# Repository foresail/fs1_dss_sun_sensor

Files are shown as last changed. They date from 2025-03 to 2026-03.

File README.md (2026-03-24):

# Foresail-1 DSS Sun Sensor

This repository contains the public available design files for the DSS sun sensor designed for the Foresail-1 Cubesat.

The performance and testing of this sensor has been documented in [this article](https://doi.org/10.1016/j.asr.2026.01.083).

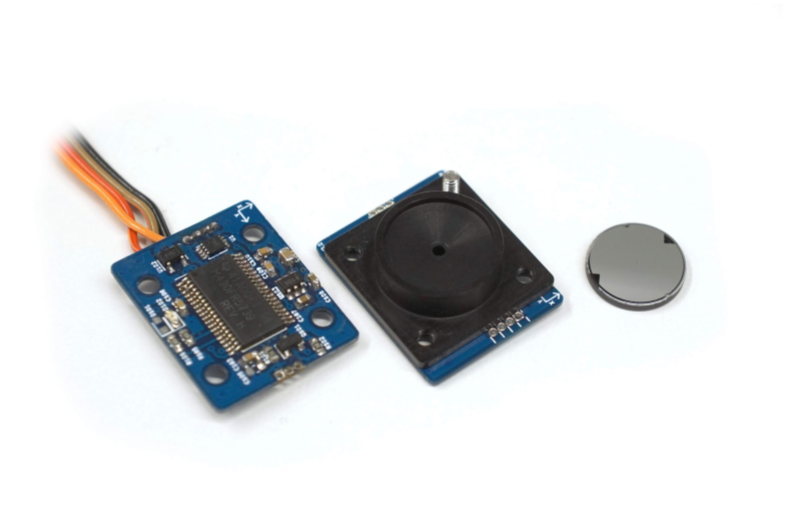
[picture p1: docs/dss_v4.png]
DSS Sun Sensor v4


The general characteristics of sensor design are:
- Dimensions: 20.4 mm × 24.8 mm × 7 mm
- Mass: 4.4 grams
- Panel mountedable into 14x14 mm hole with two M2 screws.
- Electrical connection by soldering on the panel PCB or by harness.
- FOV: ~30 degrees, resolution: 0.027°, accuracy: ±0.008°
- Refresh rate up to 38 Hz. (Sampling time: 15 ms + communication overhead)
- Can provide following data products:
    - Raw current measurements
    - Point & intensity measurements
    - Sun vector & intensity measurements
    - Angles & intensity measurements
- I2C digital serial interface (hardware version 4)
- RS-485 digital interface (hardware version 5)
- Low power consumption < 4 mW when active
- Nominal operating voltage: 3.6 - 3.8V: Can be extened easily to 2.0 – 5.5 V.

## Documentation

- [Research Paper](https://doi.org/10.1016/j.asr.2026.01.083)
- [FS1 ADCS DSS Sun Sensor Design Document](docs/FS1p_ADCS_DSS_Digital_Sun_Sensor_Hardware_Design.pdf)
- [Version 4 schematic (I2C variant)](v4/dss_v4_schema.pdf)
- [Version 4 firmware source code](v4/fw)
- [Version 5 schematic (RS-485 variant)](v5/dss_v5_schema.pdf)
- [Version 5 firmware source code](v5/fw)
- [Calibration and test tools for PC](calibration)
- [Mechanical design files](mechanical)

## Licence

The design is licenced under [CERN Open Hardware Licence Version 2](LICENCE)

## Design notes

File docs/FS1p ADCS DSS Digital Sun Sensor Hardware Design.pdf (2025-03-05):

## Digital Sun Sensor

Hardware Design v5

Responsible: Marius Anger
Version date: 2023-10-18
Page: 1 / 17

# Foresail-1p

# Digital Sun Sensor Hardware Design v5

# Aalto University

## Department of Electronics and Nanoengineering

Page: 2 / 17

### Authors

Name | Worked with parts
Bruce Clayhills | The whole document
Marius Anger | Hardware revision 5

### Table of Contents

1 General | 4
1.1 Scope | 4
1.2 Reference Documents | 4
1.3 Abbreviations and Acronyms | 5
2 Sensor Design | 5
2.1 DSS General Characteristics: | 6
2.2 Mechanical Cover | 6
2.3 ND-Filter & Mask Design | 7
2.4 Theoretical FOV | 8
2.5 Theoretical accuracy | 9
3 Electrical Design | 9
3.1 Microcontroller | 10
3.2 S9132 Profile Sensor | 11
3.3 Power Supply | 11
3.4 Inrush current | 12
3.5 Sensor Gain Selection | 14
3.6 Environment | 15
4 Software | 15
5 Calibration and Validation | 15
Appendices | 17
A. Schematics | 17
B. PCB Layout | 17

Page: 3 / 17

## 1 General

### 1.1 Scope

The purpose of this document is to present the current digital sun sensor design for Foresail-1p. This document is made for the hardware revision 5, and is mainly based on the Hamamatsu S9132 profile sensor.

The design files related to this document and version can be found on the following Github repository:
Revision 1-4: https://github.com/aaltosatellite/foresail/tree/master/dss_sunsensor
Revision 5: https://github.com/aaltosatellite/fs1p_adcs/tree/main/dss_sunsensor

### 1.2 Reference Documents

1. Hamamatsu S9132 Profile Sensor - datasheet: https://www.hamamatsu.com/resources/pdf/ssd/s9132_kmpd1075e.pdf
2. Texas Instrument’s MSP430FR5739 datasheet: http://www.ti.com/lit/ds/symlink/msp430fr5739.pdf
3. FS1 PSD Sun Sensor Design: https://docs.google.com/document/d/1SByVZYXU1UmMgaHT1f_zqc_vpBboQWTH_l9uw-Ily4A/edit# (https://docs.google.com/document/d/1SByVZYXU1UmMgaHT1f_zqc_vpBboQWTH_l9uw-Ily4A/edit#)
4. FS1 ADCS Digital Sun Sensor Software Design Document (https://docs.google.com/document/u/0/d/1WGHVzIKvUKaqTUZvLEAsgHj6r2W2jWne70urNSRBq0A/edit)
5. FS1 ADCS Digital Sun Sensor Test Plan (https://docs.google.com/document/u/0/d/1igoooQxarRuDu3o5K0XlWpgVwwoYvSnRIX3EzYSsQn4/edit)
6. ND Filter:
OD 3.0 VIS, 12.5mm Dia. Non-Reflective ND Filter (https://www.edmundoptics.eu/p/od-30-vis-125mm-dia-non-reflective-nd-filter/17996/)

### 1.3 Abbreviations and Acronyms

ADCS | Attitude Determination and Control System
DSS | Digital Sun Sensor
FOV | Field of View
MCU | MicroController Unit
ND-Filter | Neutral Density Filter
LPM | Low-Power Mode
SEM | Scanning Electron Microscope

Page: 4 / 17

## 2 Sensor Design

The digital sun sensor is based upon the Hamatsu S9132 Profile sensor. This is a CMOS based area sensor, which works with 8bit or 10bit logic (user configurable). In this board, the sensor is configured to use 8bit logic. This can however be changed at a later date with a hardware change to the PCB.

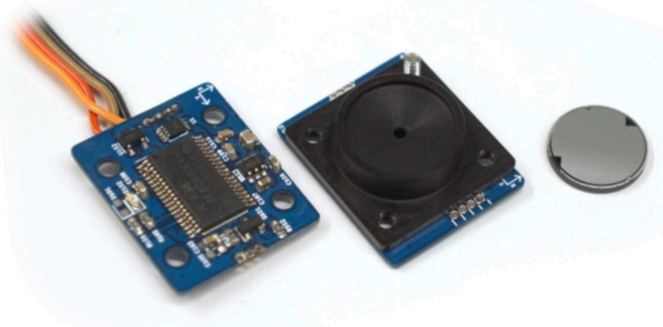
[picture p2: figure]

Figure 1. DSS PCB

The PCB of the DSS board consists of the front side, with the profile sensor, as well as the back side with the MSP430, power circuitry, RS485 transceiver and connectors to external power and programming.

The PCB design also incorporates 4×M2 mounting holes which connect the board to the cover and the hull of the satellite.

### 2.1 DSS General Characteristics:

- Dimensions: 20.4 × 24.8 × 7.0 mm
- Power consumption:
- In use: ≈100 mW
- Standby: ≈5 mW
- FOV: ≈50 degrees (Theoretical)
- Accuracy: ±0.1° (Theoretical)
- Boot up time: ≈500 ms

Page: 5 / 17

- Sampling time: ≈26 ms
- Operating voltage: 3–5 V:
- 5 V charge-pump regulator
- 3.3V LDO
- Serial Communication Interface: RS485
- ND-filter - 0.1 Transmission (%)
- Mask made with optical lithography
- 0.1 mm pinhole

### 2.2 Mechanical Cover

The DSS has an aluminum cover designed with Fusion 360. This mechanical cover provides protection to the S9132 sensor, as well as houses the ND-filter and mask inside. The cover will be made of space grade aluminum, which is anodized black.

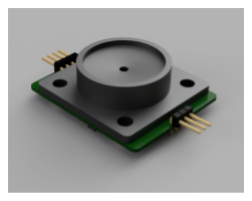
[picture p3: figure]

Figure 3. DSS Cover v4

The mask of the DSS is put on top of the ND-filter. The DSS cover has been designed with minimal tolerances, so that there is little to none excess space for the ND filter to move around. However, the tolerances in the design assume the worst case scenario for the dimensions of the ND-filter and S9132 profile sensor.

To ensure that the ND-filter and mask stays in one spot, the ND-filter will be glued to the aluminum cover using two part space grade epoxy glue. It is important to perform all the testing procedures defined in the FS1 ADCS Digital Sun Sensor Prototype Test Plan (https://drive.google.com/open?id=1igoooQxarRuDu3o5K0XlWpgVwwoYvSnRIX3EzYSsQn4) document after this, to ensure the correct calibration values and proper operation of the sensor.

For the manufacturing of the mechanical structure and the PCB of the sun sensor be sure to take a look at the FS1 ADCS Digital Sun Sensor Manufacturing Guide. (https://drive.google.com/open?id=1_A-BLVwWmDk6d4qx7FV5U0ANPm-P0pnfzcUZG10FYfE)

### 2.3 ND-Filter & Mask Design

The S9132 requires an ND-filter to reduce the intensity of the light hitting the surface of the sensor, otherwise the sensor will saturate and output values of maximum intensity. This results in loss of accuracy, once the center point of the light hitting the surface of the sensor is estimated.

The sensor must be able to withstand the intensity of light in the visual spectrum (to which it is most sensitive) while operating in space. The calculated ND-filter transmittance value should be

Page: 6 / 17

around 0.1, in order to prevent saturation.

This is done with an Edmund Optics OD 3.0 VIS, 12.5mm Dia. Non-Reflective ND Filter, (https://www.edmundoptics.eu/p/od-30-vis-125mm-dia-non-reflective-nd-filter/17996/) with a transmittance value of 0.1. The transmittance value is guaranteed to be within a tolerance of ±0.05% by the manufacturer. This value will also be verified during the EQM and flight model testing and characterization.

The mask design is a simple pinhole in the middle of the ND-filter with a hole of a diameter of 0.1 mm as shown in Figure 4. This shows an incoming incident light hitting the profile sensor surface. The ND-filter also provides additional UV-protection to the profile sensor.

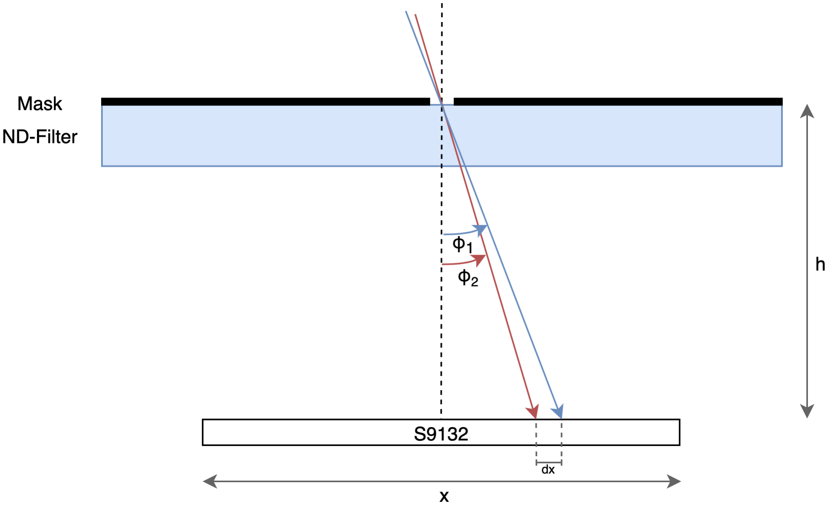
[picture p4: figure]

Figure 4. ND-filter & Mask

The film, which is set on top of the ND-filter, will have a titanium coating laid directly onto the glass surface with optical lithography. The titanium adheres strongly onto the glass layer, providing a strong bond. After this, an additional layer of aluminium will also be set on top of the layer of titanium, in order to provide better resistance to physical damage from sunlight and other sources. The aluminium also adheres better to a titanium surface compared to glass directly.

The diameter of the pinhole can be seen in Figure 5. This is an image taken with a SEM.

Page: 7 / 17

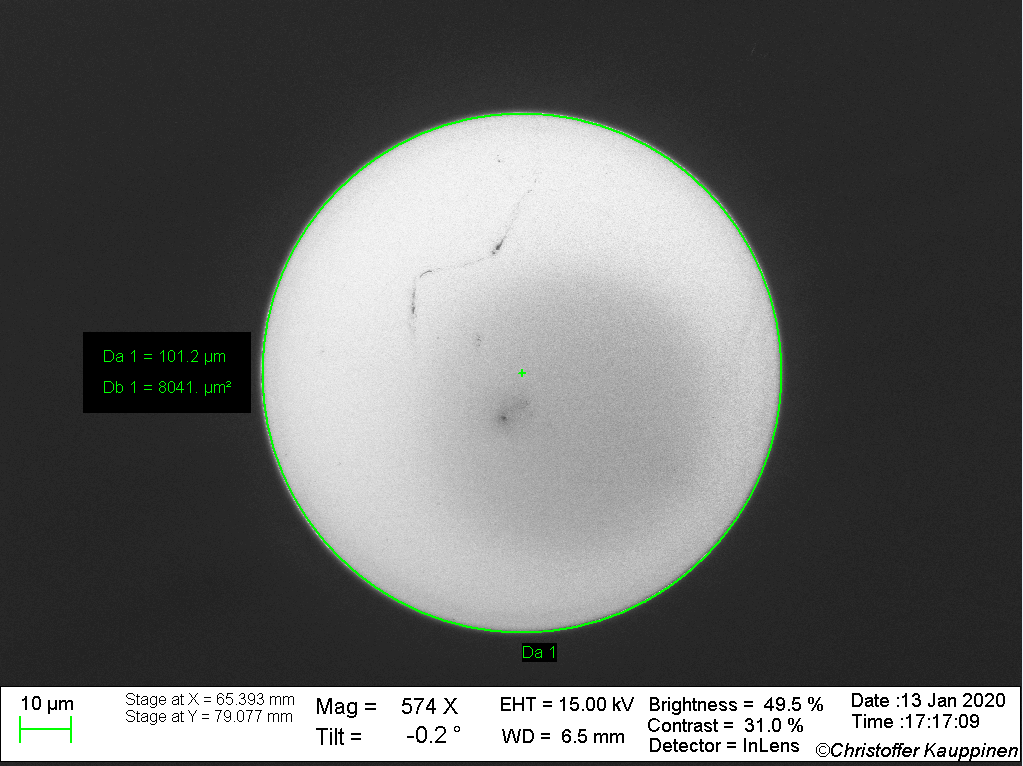
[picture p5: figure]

Figure 5. SEM picture of the pinhole

### 2.4 Theoretical FOV

The field of view (FOV) of a sun sensor is an integral part of its design, and a defining quality of the sensor. Different satellite designs have different requirements that the sun sensors must achieve. There is always a trade-off between the maximum theoretical accuracy and the FOV of a sun sensor.

The selection of the FOV of a sun sensor should be made in conjunction with the selection of the desired accuracy of the sensor. In addition to the theoretical analysis for these properties, one should also take into account the practical limitations of the hardware on the sensor.

The FOV of a pinhole-based sun sensor is affected by the height of the mask from the sensor's surface, the location of the pinhole relative to the center spot of the sensor and the physical constraints of the enclosure. The equation governing the maximum theoretical FOV of a sun sensor is:

, where is the height of the pinhole from the sensor surface and x array length of the sensor.

### 2.5 Theoretical accuracy

Page: 8 / 17

The accuracy of a sun sensor is not a property that should be addressed alone, as the FOV impacts the theoretical accuracy and vice versa. A higher pinhole height leads to a better accuracy, as the FOV is limited. This is because the sensor has a finite amount of pixels, which are used for measurements. So a smaller FOV in theory equates to a better accuracy as the sensor can utilise more pixels to distinguish a variation of one degree.

The linear resolution is the distance in between the individual pixels on the profile sensor. The accuracy of a sun sensor can be derived from the pinhole height and the linear resolution of the
sensor. Referring to Figure 4, the accuracy is the difference between | and , when | is equal to
the linear resolution. This gives us the following relation for the maximum theoretical accuracy:

The equation, which relates the FOV and the accuracy of a sun sensor is:

, where is the array size and is the linear resolution.

Page: 9 / 17

## 3 Electrical Design

The electrical design of the sun sensor has been done in KiCad 5.0. Key design objectives have been a reduced power consumption, and the reliable operation of the sensor board.

### 3.1 Microcontroller

The DSS has a Texas Instruments MSP430FR5739 microcontroller embedded into its design, operated at 24 MHz, which handles data processing and interfacing with the rest of the ADCS on-board the OBC.

If needed, the MCU can also be operated at a lower frequency to reduce power consumption.

MCU characteristics:
- 16-Bit RISC Architecture up to 24-MHz Clock
- –40°C to +85°C Operation
- 16 KB of Nonvolatile FRAM Memory
- RS485 communication protocol
- 2.0 V to 3.6 V operating voltage

The MCU also has an integrated watch-dog timer (WDT), which ensures that the MCU is rebooted if it detects a halt in the main loop if code execution lingers for longer than a certain time period. The WDT will be used to prevent a situation, where the sensor becomes unresponsive, due to a fault in the MCU.

This WDT has not yet been implemented on the DSS.

### 3.2 S9132 Profile Sensor

The S9132 profile sensor is a CMOS area sensor, which provides 8-bit data to the MCU. This data is provided in the form of two histograms, which each contain the profile sensor data from the x-and y-axis.

The profile sensor spectral response can be seen in Figure 6. The spectral response shows that the sensor is most sensitive to light in the visible spectrum (≈500–700nm).

Page: 10 / 17

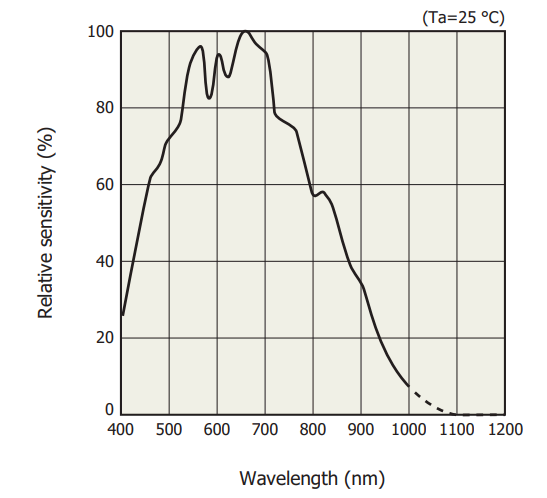
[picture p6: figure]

Figure 6. S9132 Spectral Response

The S9132 profile sensor can be used with a frequency up to 10 MHz in 8-bit mode, with a rated power usage of 75 mW. The analog supply voltage of the sensor must be ≈5 V, while the digital logic side supply voltage can vary between 3–5 V. The digital supply voltage is supplied from the same LDO circuit on the board. This is to ensure the same digital signal levels for the sensor and MCU, so that they can communicate with each other as the MCU is not 5 V tolerant.

### 3.3 Power Supply

For power, the board has a boost DC/DC charge-pump converter, which transforms the incoming 3.6 V satellite bus voltage into the 5 V needed by the S9132 profile sensor. A low-dropout regulator (LDO) provides the 3.3 V power input for the MCU. This is also directly converted down from the bus voltage.

Additionally bypass capacitors are set to reduce ripple in the 5 V power line. With a 10 uF 0805 bypass capacitor on the output of the charge-pump, it is possible to reduce the largest deviation in voltage down to 39m V @5 V (from around 100 mV).

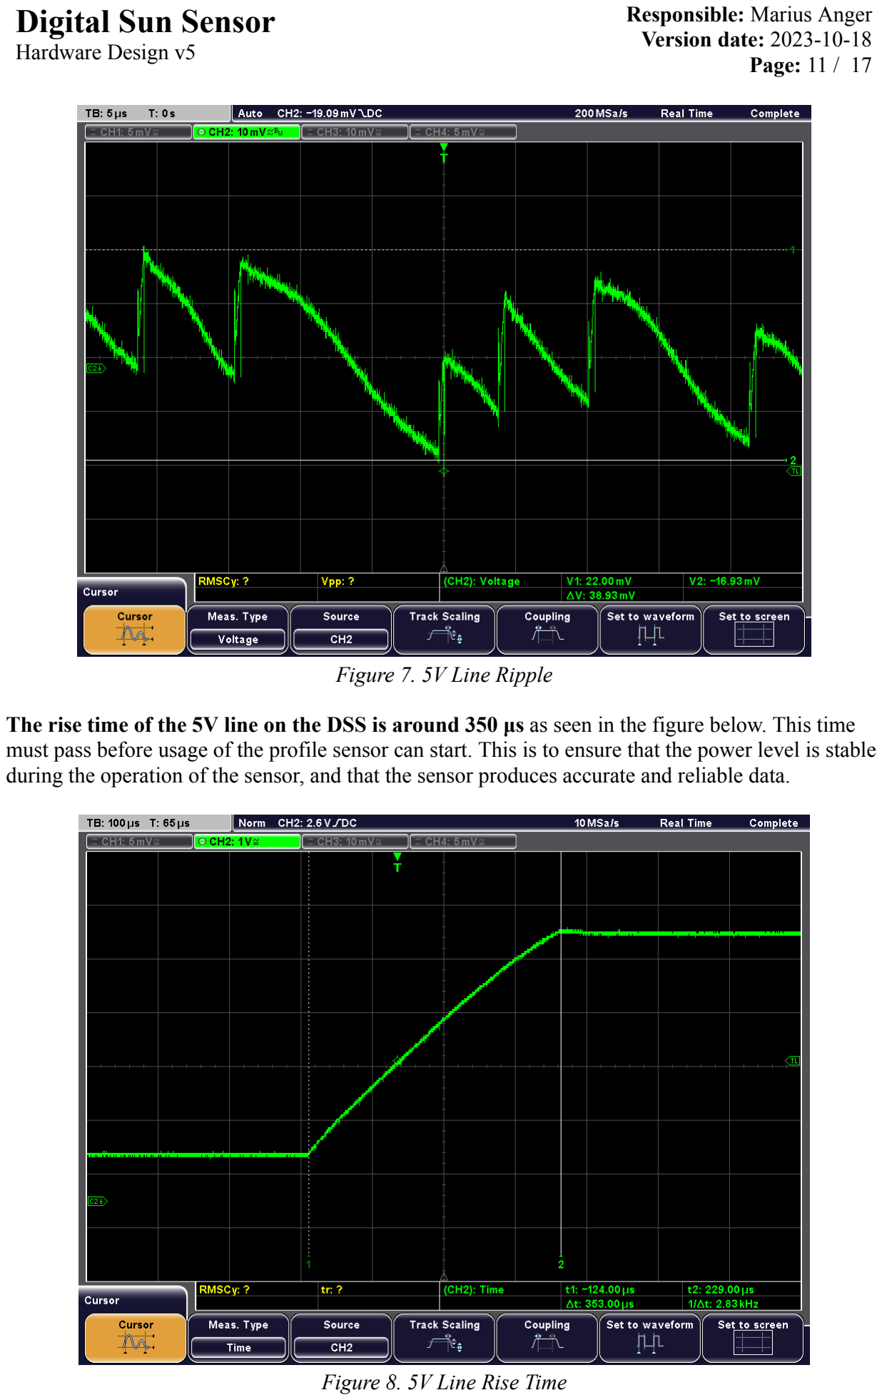
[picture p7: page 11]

Page: 11 / 17

Figure 7. 5V Line Ripple

The rise time of the 5V line on the DSS is around 350 μs as seen in the figure below. This time must pass before usage of the profile sensor can start. This is to ensure that the power level is stable during the operation of the sensor, and that the sensor produces accurate and reliable data.

Figure 8. 5V Line Rise Time

Page: 12 / 17

### 3.4 Inrush current

Inrush current of the DSS was measured using an external LTC4368 circuit, which is also used in other subsystems of the satellite. The DSS is capable of shutting down and powering back up the profile sensor in an effort to reduce power consumption while not in use. However, due to the high capacitance of the boost regulator output line, there is a large inrush current while powering up the profile sensor. The figure below shows the inrush current of the device, while applying a voltage of 3.6V.

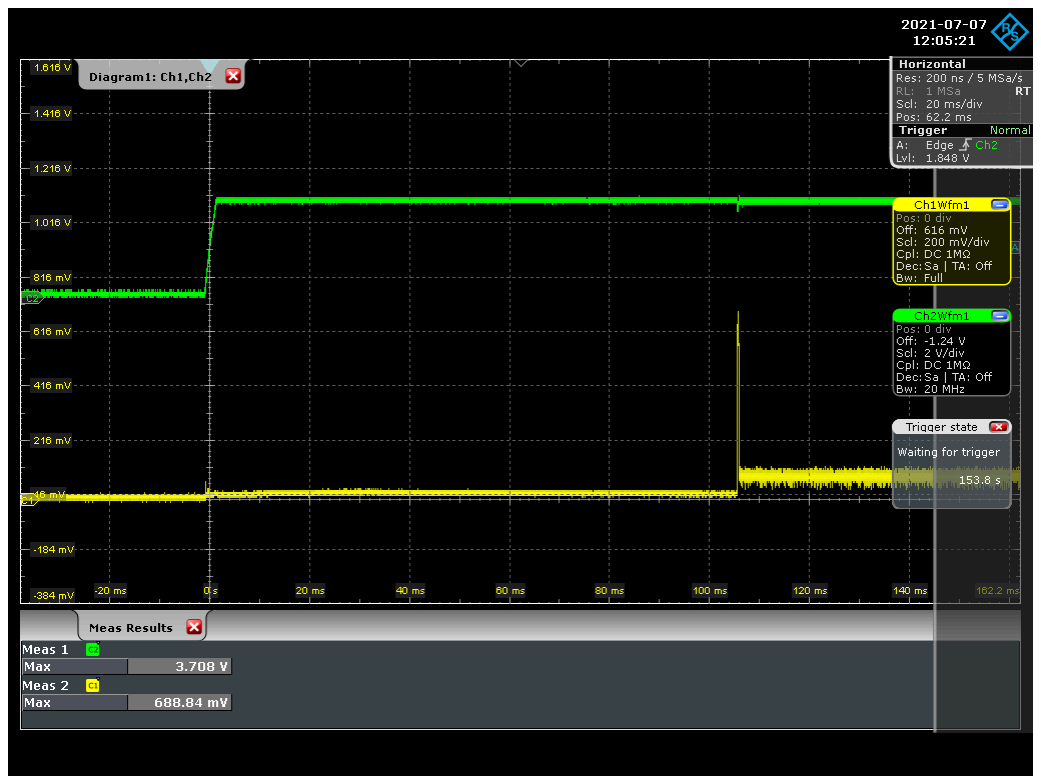
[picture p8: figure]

Figure . DSS Inrush current

The DSS was set up to wait for approximately 100ms prior to enabling the boost converter, which runs the profile sensor. From the Figure above it can be seen that the maximum voltage of the current sense line was 689mV, which equates to an inrush current of approximately 276mA when the boost converter is enabled.

Needless to say the inrush current of the DSS is far too high for the system with the current configuration. The output capacitance of the boost converter output line is 10uF, which is most likely the source of this spike in current consumption. Action should be taken to mitigate and limit the effects of this behavior.

Unfortunately reducing the capacitance of the output line will increase the output voltage ripple, as discussed in the previous subsection. Thus, in order to fix the issue, a different boost converter is needed, or the system must be configured to provide the current necessary to overcome this inrush current.

The Voltage/Inrush current relationship was also examined for the 5V line on the DSS. The result can be seen from the Figure below.

Page: 13 / 17

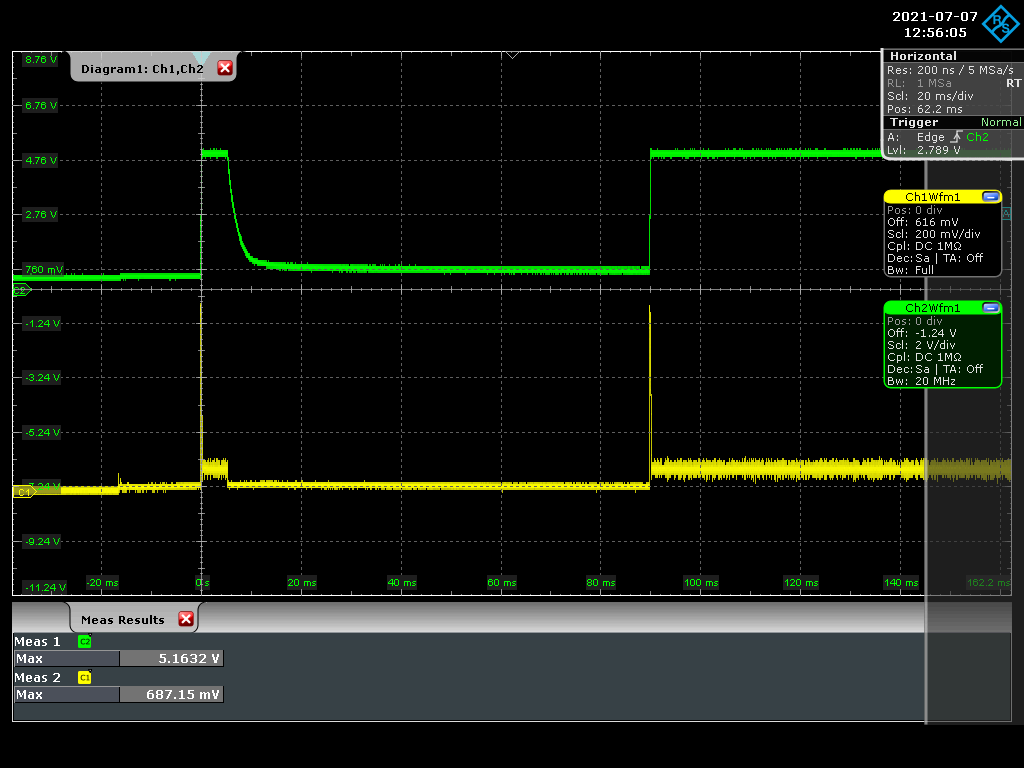
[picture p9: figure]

Figure . 5V Inrush current

During initial start-up, the MSP430 does not pull down the boost enable pin, which results in an inrush current spike during power-on. To prevent this unwanted behavior, a pulldown resistor should be added on the boost enable line.

Examining the inrush current of the 5V line a little closer, we can determine the ramp rate of the voltage line and the inrush current during this stage. The 5V line in comparison to the current consumption can be seen from the Figure below.

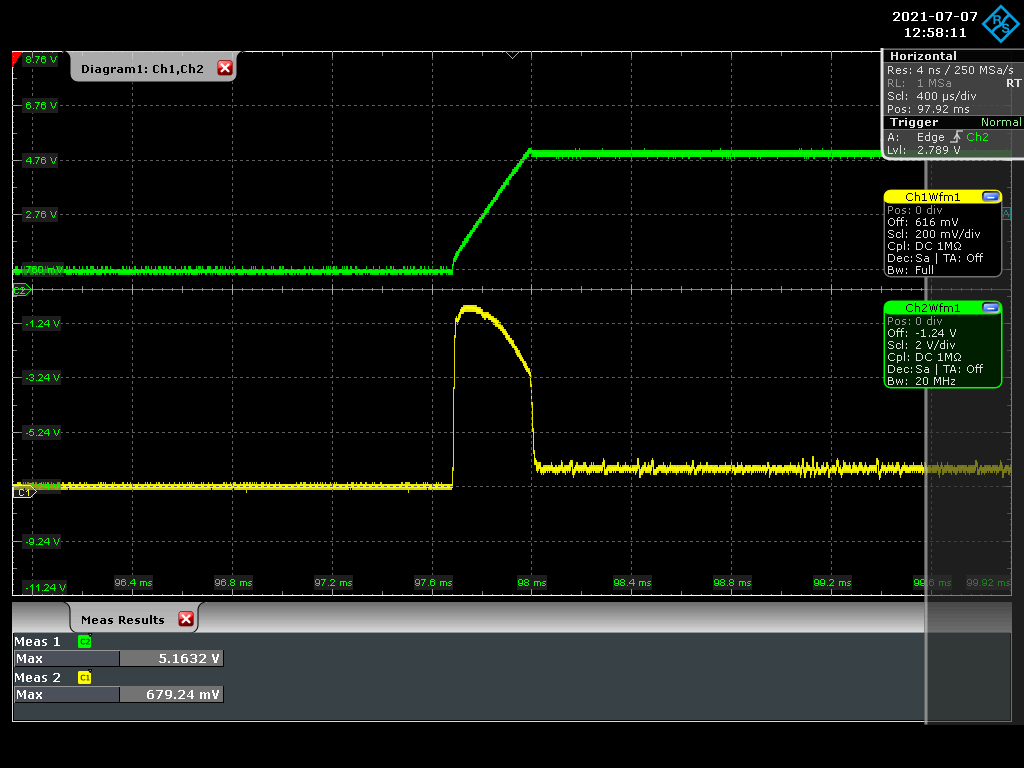
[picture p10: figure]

Figure . 5V Ramp-up

As can be seen from the Figure above, the inrush current spikes immediately after voltage is applied

Page: 14 / 17

to the line and starts decreasing, while the voltage ramps up. This suggests that we are able to limit the inrush current by slowing down the ramp-up rate of the 5V line. This can be accomplished with an external MOSFET circuit.

### 3.5 Sensor Gain Selection

The S9132 has a controllable hardware sensor gain setting for both x- and y-axes. The gain affects the sensor's sensitivity to light. A 5V digital signal line is required to control the gain on the S9132, this command is provided by the MCU on the board.

The MSP430 however is not 5 V tolerant and thus is not capable of providing the needed voltage. To solve this, the gain setting is controlled by the MCU via an N-channel MOSFET, which drives the voltage on the gain pin from a logical high to a logical low through a pull-up resistor.

### 3.6 Environment

The table shows the maximum recommended operating temperatures specified by the manufacturers of the components.

Table 1. Environment Characteristics
Part | Recommended Operating Temperature Range
Hamamatsu S9132 Profile Sensor | −5°C to +65°C
MSP430FR5739 Microcontroller | −40°C to +85°C
TLV733P-3.3V | −40°C to +150°C
THVD14xx | −40°C to 125°C

Page: 15 / 17

## 4 Software

The software design of the Digital Sun Sensor is documented in the FS1p ADCS Digital Sun Sensor Software Design. (https://docs.google.com/document/u/0/d/1WGHVzIKvUKaqTUZvLEAsgHj6r2W2jWne70urNSRBq0A/edit) This includes the overall architecture, algorithms and interfacing guide.

Page: 16 / 17

## 5 Calibration and Validation

The calibration and validation of the digital sun sensor is documented in the FS1 ADCS Digital Sun Sensor Prototype Test Plan (https://drive.google.com/open?id=1igoooQxarRuDu3o5K0XlWpgVwwoYvSnRIX3EzYSsQn4) document.

Tests and calibrations are performed with python scripts. A host Windows computer is used to communicate with the DSS through a FTDI RS485 cable. The scripts that run calibration and testing of the DSS can be found on the Github repository at the following location: https://github.com/aaltosatellite/fs1p_adcs/tree/main/testing_scripts

Additionally the unit test system can be used to perform a basic functional test after manufacturing. https://github.com/aaltosatellite/fs1p_tests/blob/main/egse_tests/test_sunsensor.py

## Appendices

Page: 17 / 17

### PCB Layout

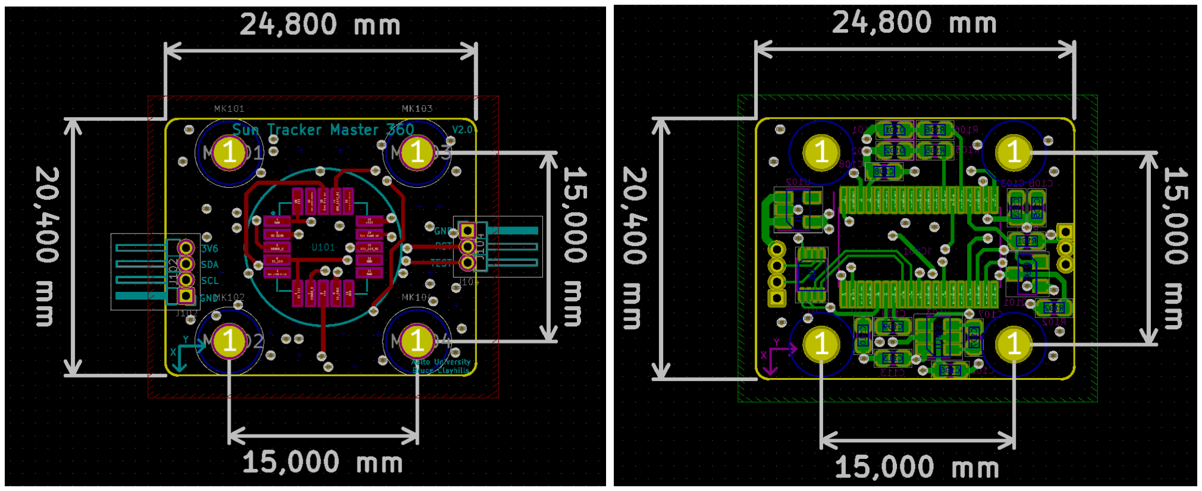
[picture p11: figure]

Dimensions: | 24.80 x 20.40 mm
Mounting Hole Spacing: | 15 mm
PCB Thickness: | 0.8 mm

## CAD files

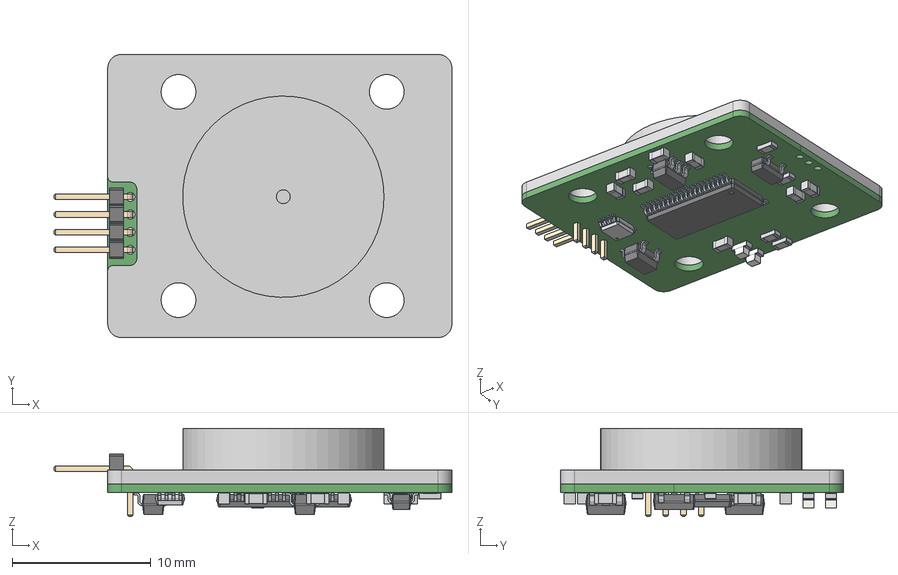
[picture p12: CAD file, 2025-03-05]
mechanical/digital_sunsensor.step
28.7 x 20.4 x 6.35 mm
Cover

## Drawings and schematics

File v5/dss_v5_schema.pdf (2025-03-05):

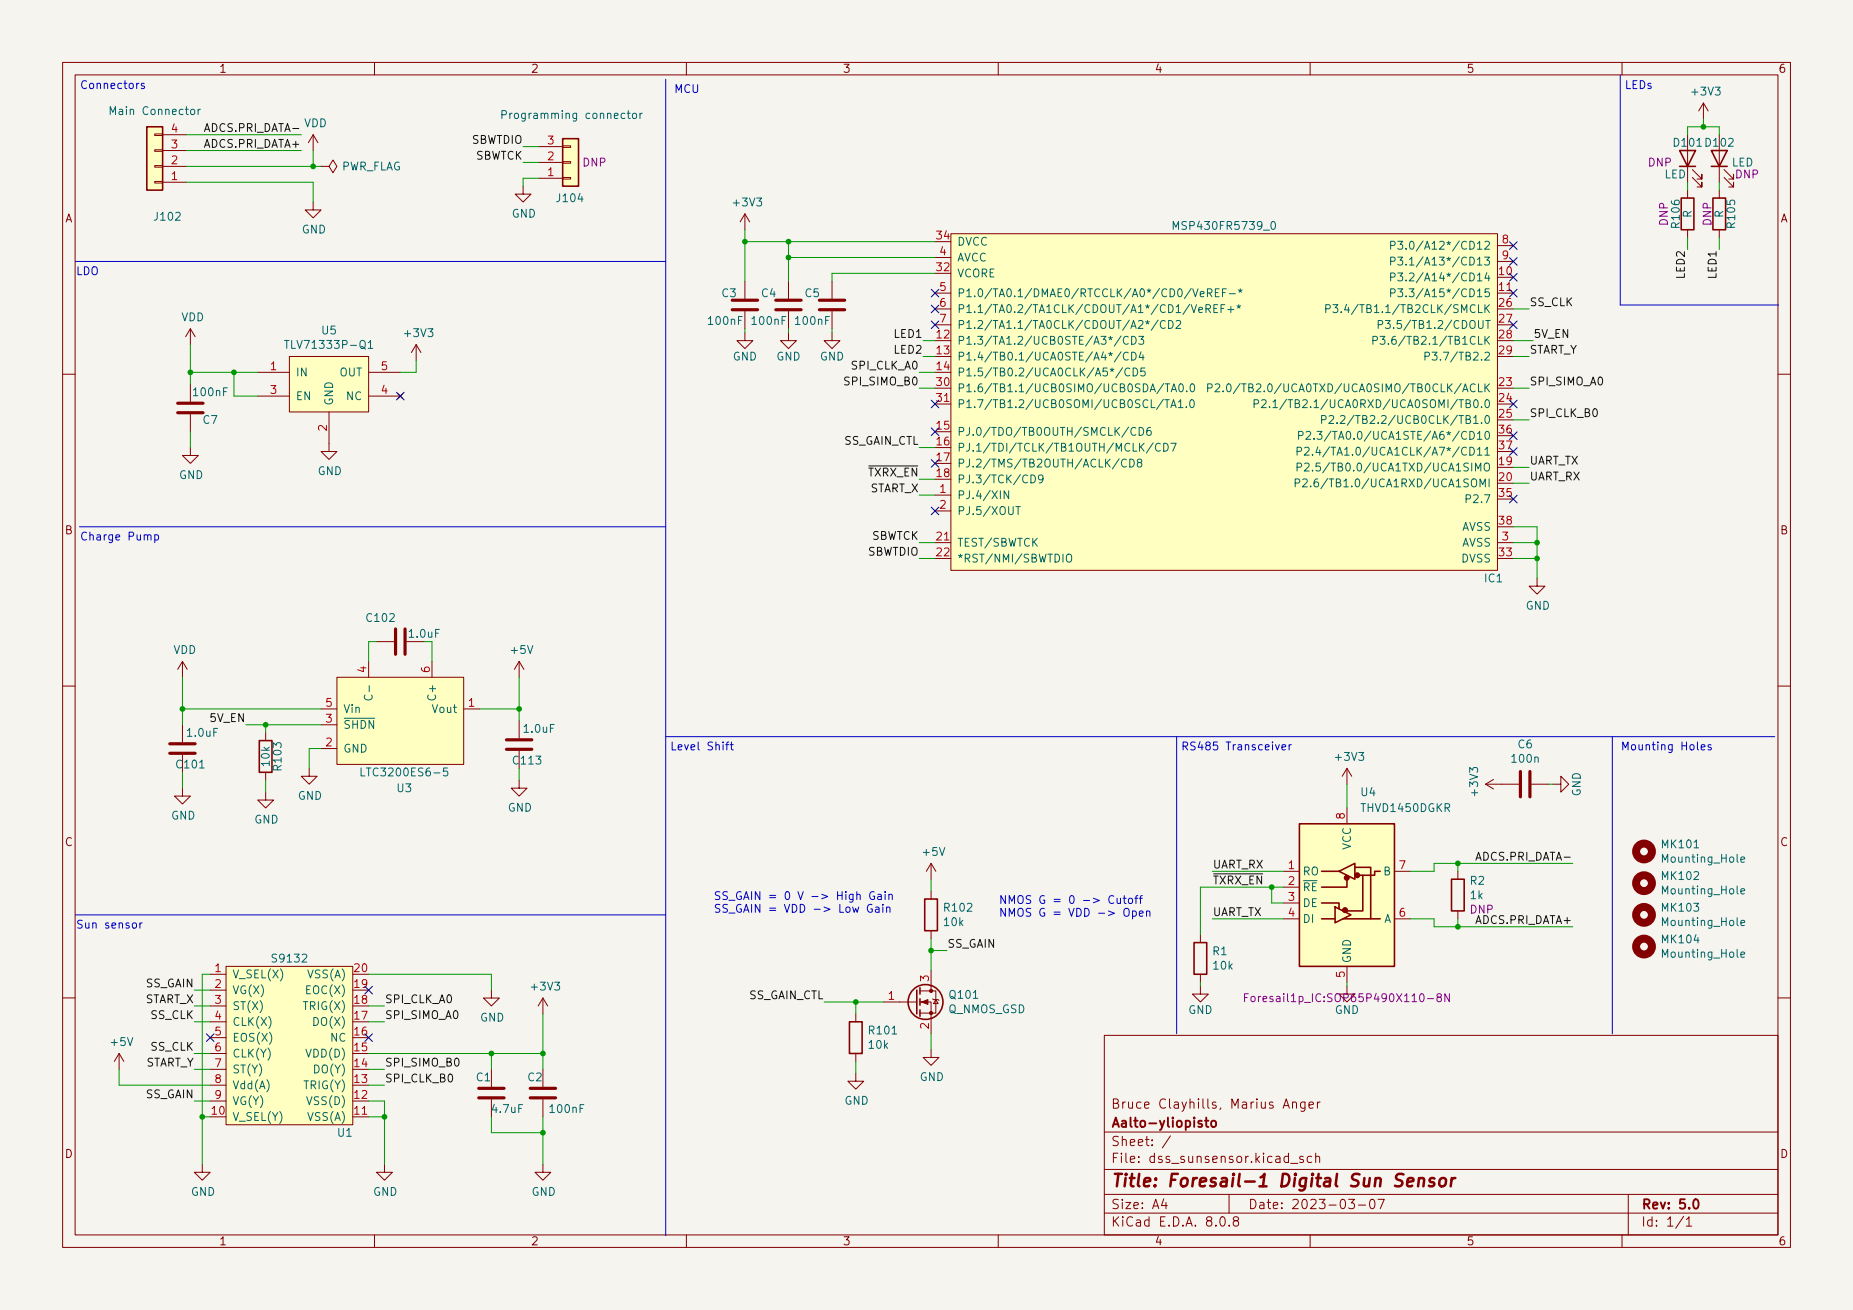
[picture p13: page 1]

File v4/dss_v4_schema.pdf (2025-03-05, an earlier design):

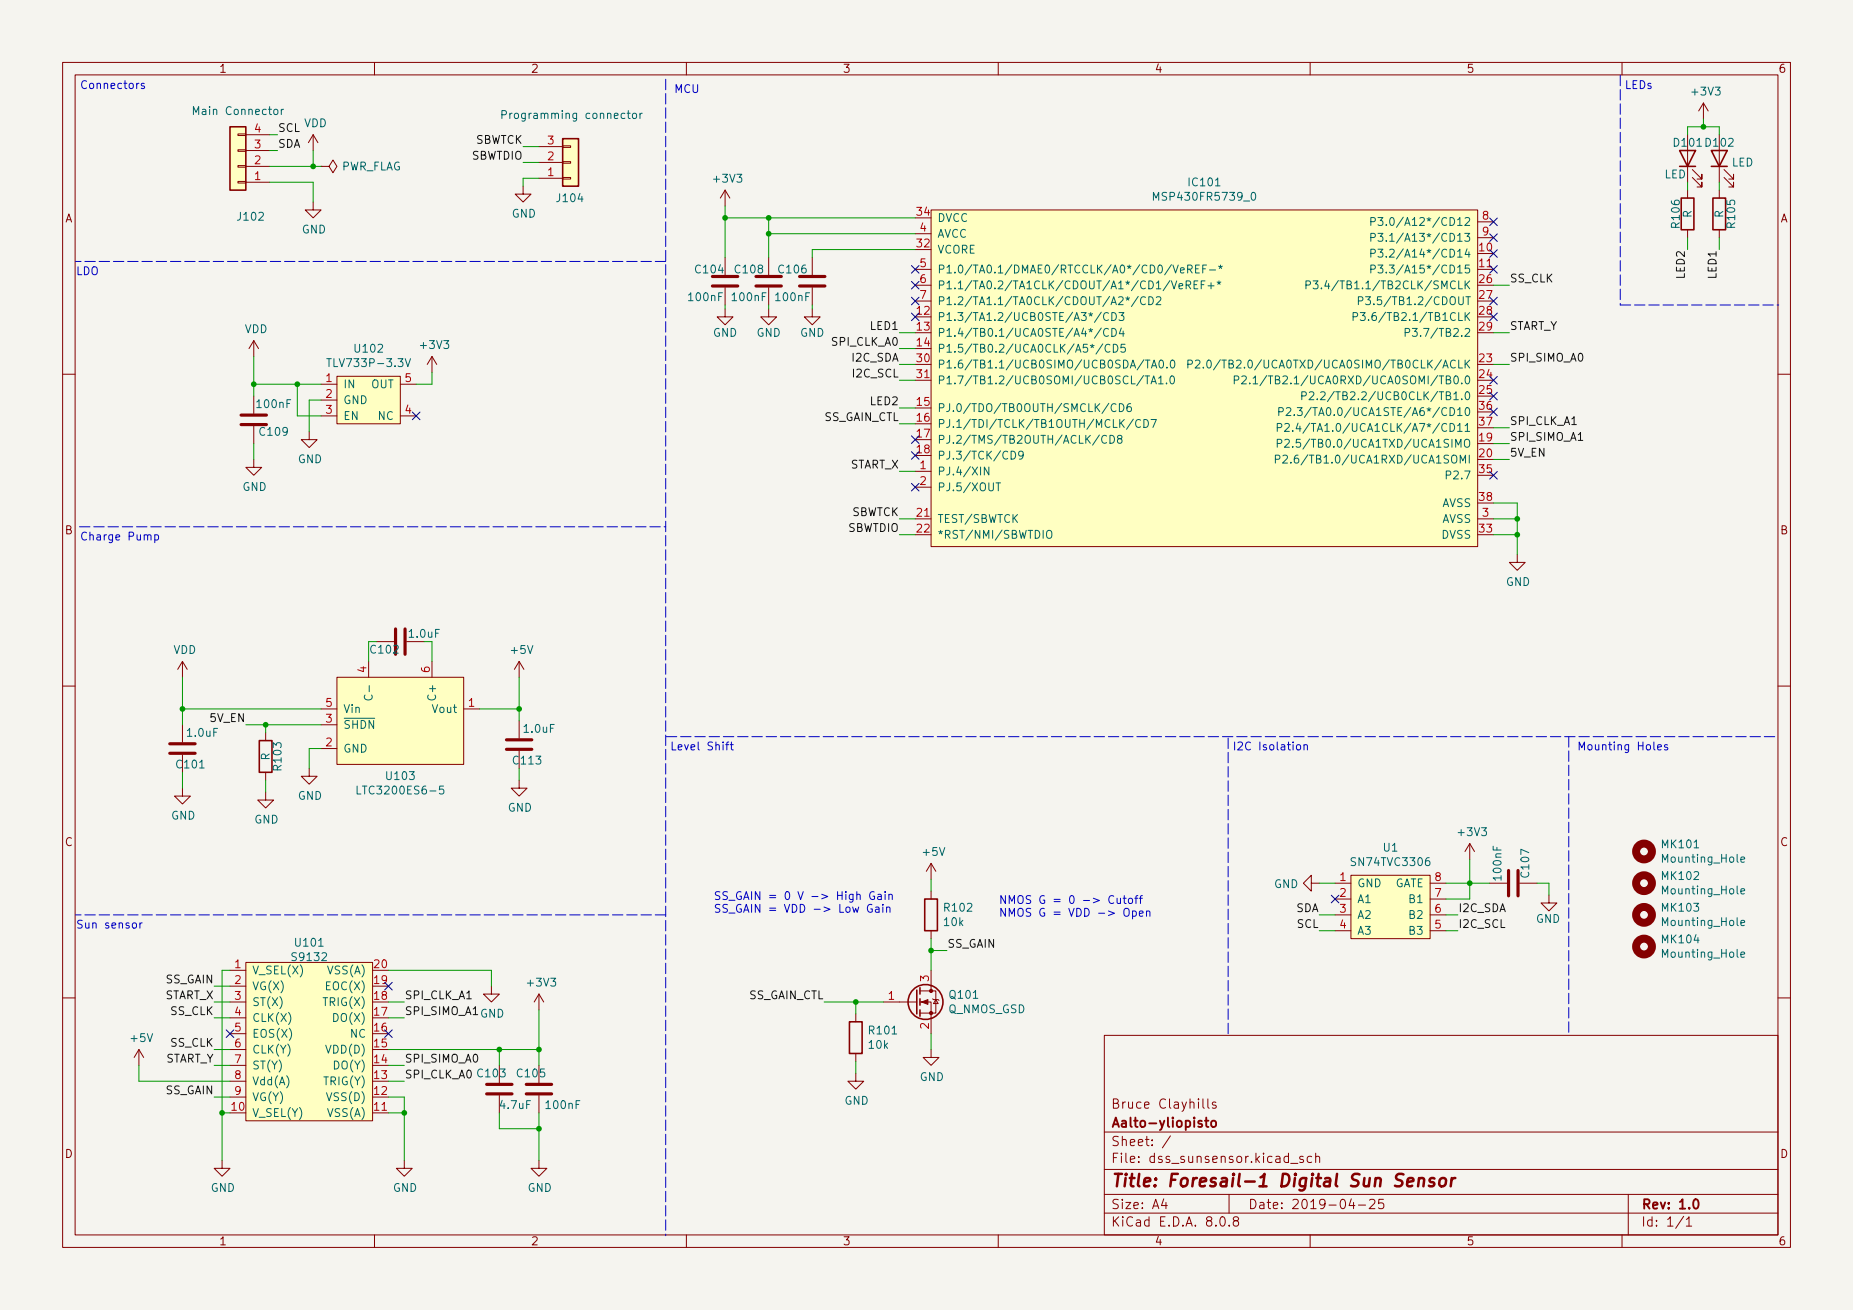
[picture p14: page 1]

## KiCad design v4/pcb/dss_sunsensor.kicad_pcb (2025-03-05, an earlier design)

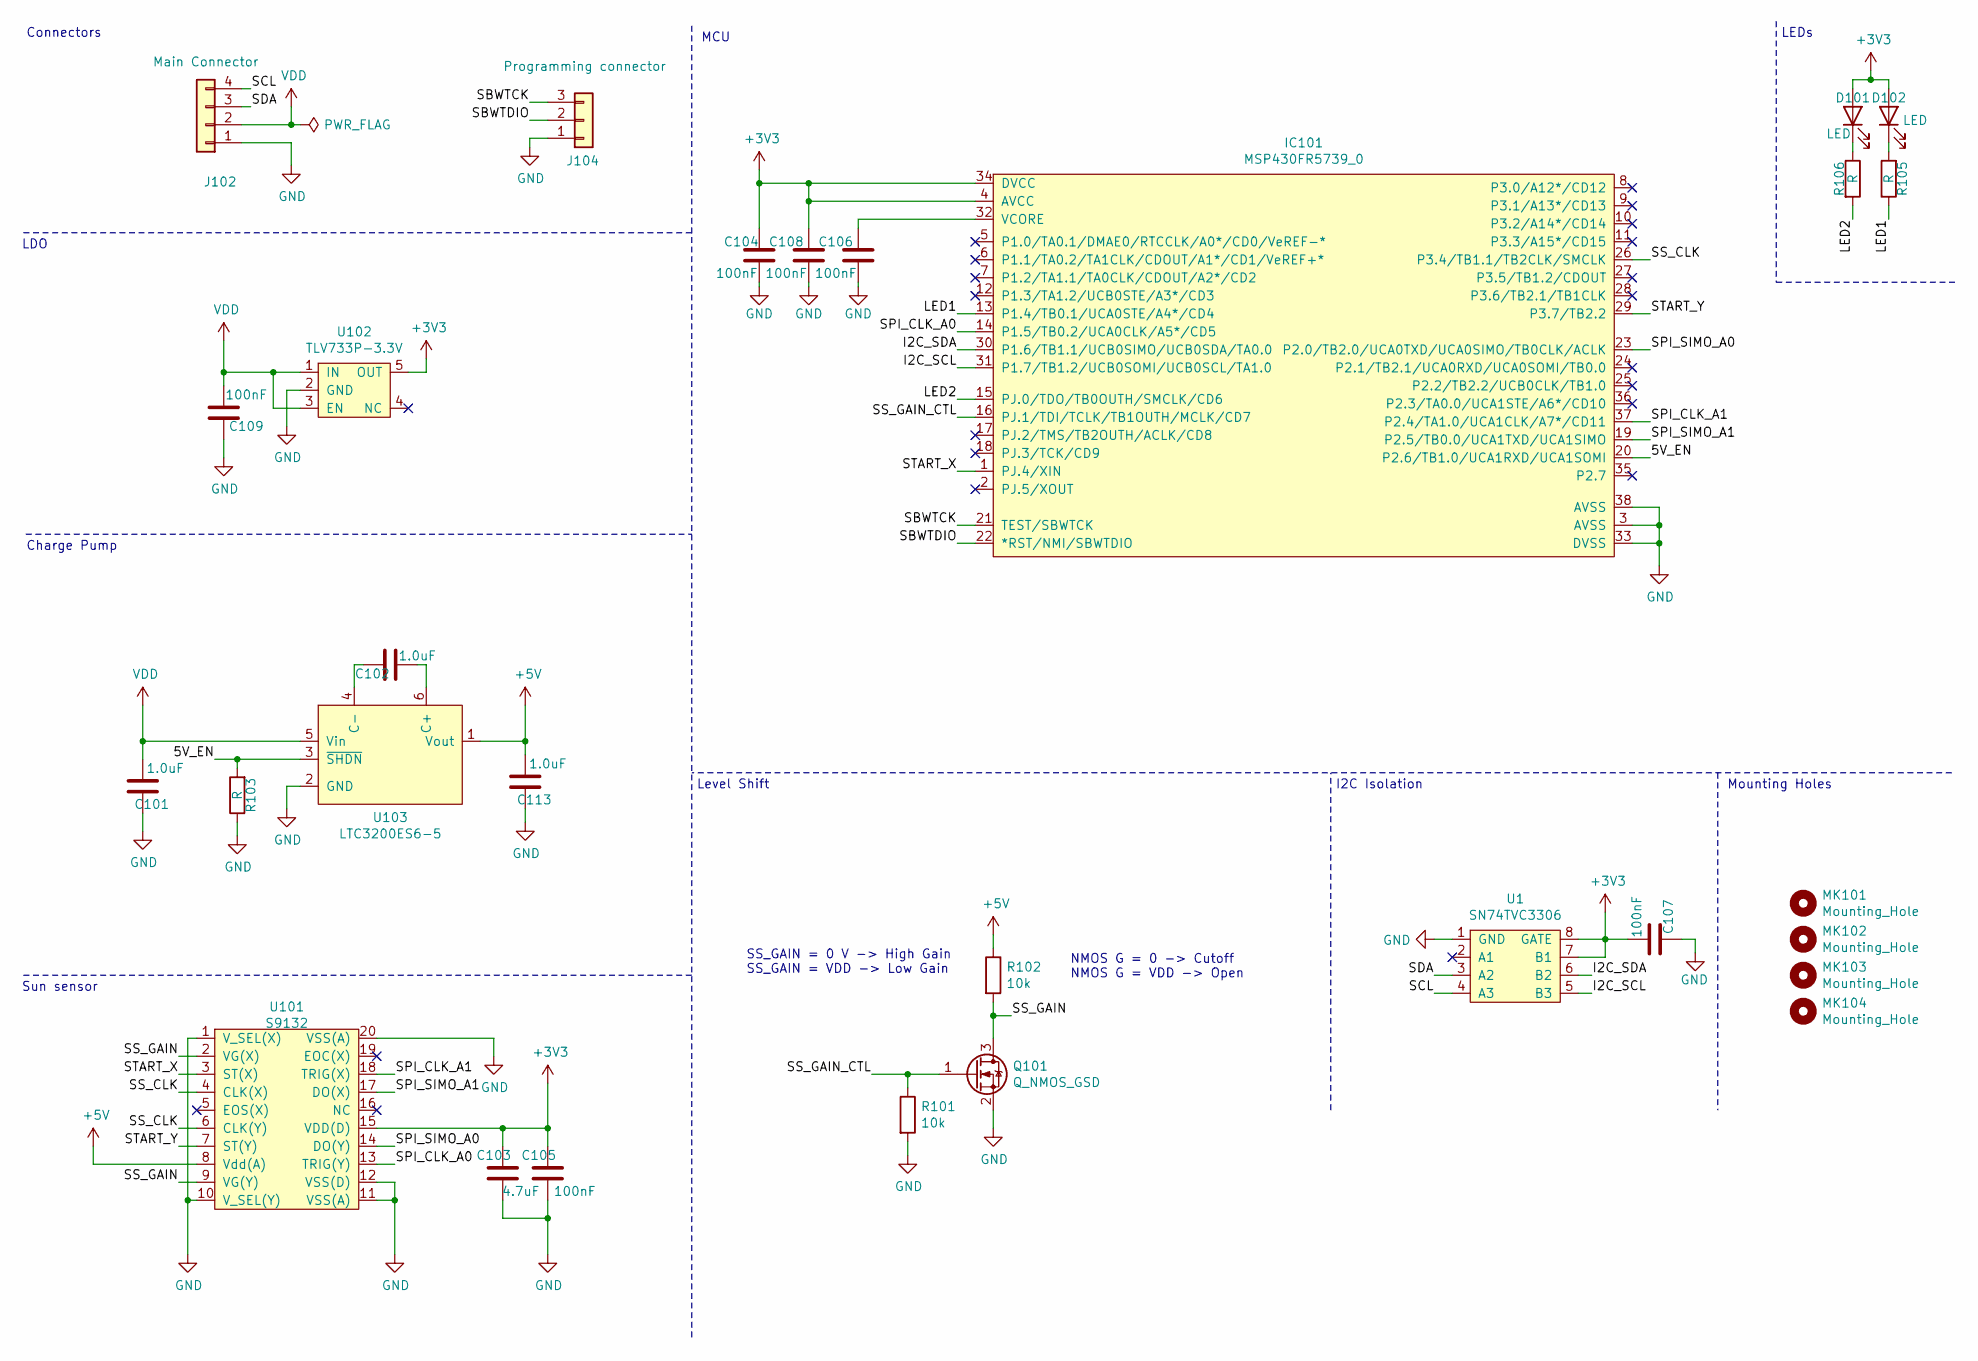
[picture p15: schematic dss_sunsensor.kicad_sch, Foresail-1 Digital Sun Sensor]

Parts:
C101, C102, C113: 1.0uF; C_0603_1608Metric
C103: 4.7uF; C_0603_1608Metric
C104, C105, C106, C107, C108, C109: 100nF; C_0402_1005Metric
D101, D102: LED; LED_0603_1608Metric
IC101: MSP430FR5739_0; TSSOP-38_6.1mm
J102: Main Connector; PinHeader_1x04_P1.27mm_Horizontal
J104: Programming connector; PinHeader_1x03_P1.27mm_Horizontal
MK101, MK102, MK103, MK104: Mounting_Hole; MountingHole_2.2mm_M2
Q101: Q_NMOS_GSD; SOT-23
R101, R102: 10k; R_0402_1005Metric
R103, R105, R106: R; R_0402_1005Metric
U1: SN74TVC3306; VSSOP-8_2.4x2.1mm_P0.5mm
U101: S9132
U102: TLV733P-3.3V; SOT-23-5
U103: LTC3200ES6-5; SOT-23-6

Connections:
+3V3: C103.2, C104.2, C105.2, C107.1, C108.2, D101.2 (A), D102.2 (A), IC101.4 (AVCC), IC101.34 (DVCC), U1.7 (B1), U1.8 (GATE), U101.15 (VDD(D)), U102.5 (OUT)
+5V: C113.1, R102.1, U101.8 (Vdd(A)), U103.1 (Vout)
/5V_EN: IC101.20 (P2.6/TB1.0/UCA1RXD/UCA1SOMI), R103.2, U103.3 (~SHDN)
/I2C_SCL: IC101.31 (P1.7/TB1.2/UCB0SOMI/UCB0SCL/TA1.0), U1.5 (B3)
/I2C_SDA: IC101.30 (P1.6/TB1.1/UCB0SIMO/UCB0SDA/TA0.0), U1.6 (B2)
/LED1: IC101.13 (P1.4/TB0.1/UCA0STE/A4*/CD4), R105.1
/LED2: IC101.15 (PJ.0/TDO/TB0OUTH/SMCLK/CD6), R106.2
/SBWTCK: IC101.21 (TEST/SBWTCK), J104.3
/SBWTDIO: IC101.22 (*RST/NMI/SBWTDIO), J104.2
/SCL: J102.4, U1.4 (A3)
/SDA: J102.3, U1.3 (A2)
/SPI_CLK_A0: IC101.14 (P1.5/TB0.2/UCA0CLK/A5*/CD5), U101.13 (TRIG(Y))
/SPI_CLK_A1: IC101.37 (P2.4/TA1.0/UCA1CLK/A7*/CD11), U101.18 (TRIG(X))
/SPI_SIMO_A0: IC101.23 (P2.0/TB2.0/UCA0TXD/UCA0SIMO/TB0CLK/ACLK), U101.14 (DO(Y))
/SPI_SIMO_A1: IC101.19 (P2.5/TB0.0/UCA1TXD/UCA1SIMO), U101.17 (DO(X))
/SS_CLK: IC101.26 (P3.4/TB1.1/TB2CLK/SMCLK), U101.4 (CLK(X)), U101.6 (CLK(Y))
/SS_GAIN: Q101.3 (D), R102.2, U101.2 (VG(X)), U101.9 (VG(Y))
/SS_GAIN_CTL: IC101.16 (PJ.1/TDI/TCLK/TB1OUTH/MCLK/CD7), Q101.1 (G), R101.1
/START_X: IC101.1 (PJ.4/XIN), U101.3 (ST(X))
/START_Y: IC101.29 (P3.7/TB2.2), U101.7 (ST(Y))
GND: C101.2, C103.1, C104.1, C105.1, C106.1, C107.2, C108.1, C109.2, C113.2, IC101.3 (AVSS), IC101.33 (DVSS), IC101.38 (AVSS), J102.1, J104.1, Q101.2 (S), R101.2, R103.1, U1.1 (GND), U101.1 (V_SEL(X)), U101.10 (V_SEL(Y)), U101.11 (VSS(A)), U101.12 (VSS(D)), U101.20 (VSS(A)), U102.2 (GND), U103.2 (GND)
unnamed: C102.1, U103.6 (C+)
unnamed: C102.2, U103.4 (C-)
unnamed: C106.2, IC101.32 (VCORE)
unnamed: D101.1 (K), R106.1
unnamed: D102.1 (K), R105.2
VDD: C101.1, C109.1, J102.2, U102.1 (IN), U102.3 (EN), U103.5 (Vin)

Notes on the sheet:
LDO
Mounting Holes
SS_GAIN = 0 V -> High Gain SS_GAIN = VDD -> Low Gain
Charge Pump
Sun sensor
NMOS G = 0 -> Cutoff NMOS G = VDD -> Open
Connectors
Level Shift
LEDs
MCU
I2C Isolation

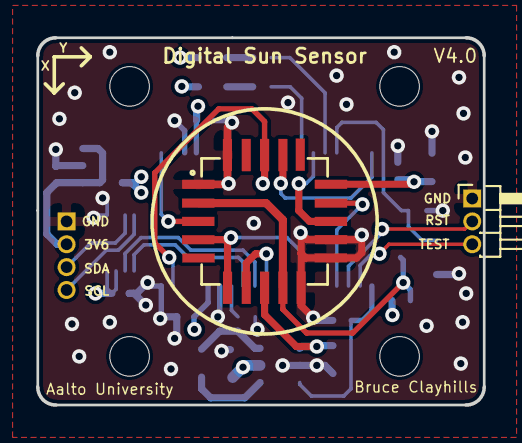
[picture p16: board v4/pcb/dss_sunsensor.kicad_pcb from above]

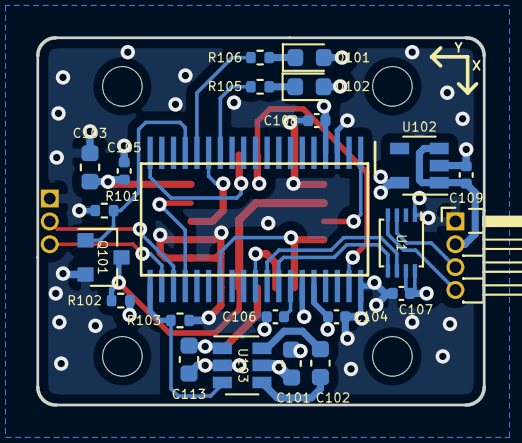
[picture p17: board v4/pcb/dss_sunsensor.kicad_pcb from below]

Board: 4 copper layers, 24.8 x 20.4 mm, 29 parts (23 on the bottom side), 27 nets.

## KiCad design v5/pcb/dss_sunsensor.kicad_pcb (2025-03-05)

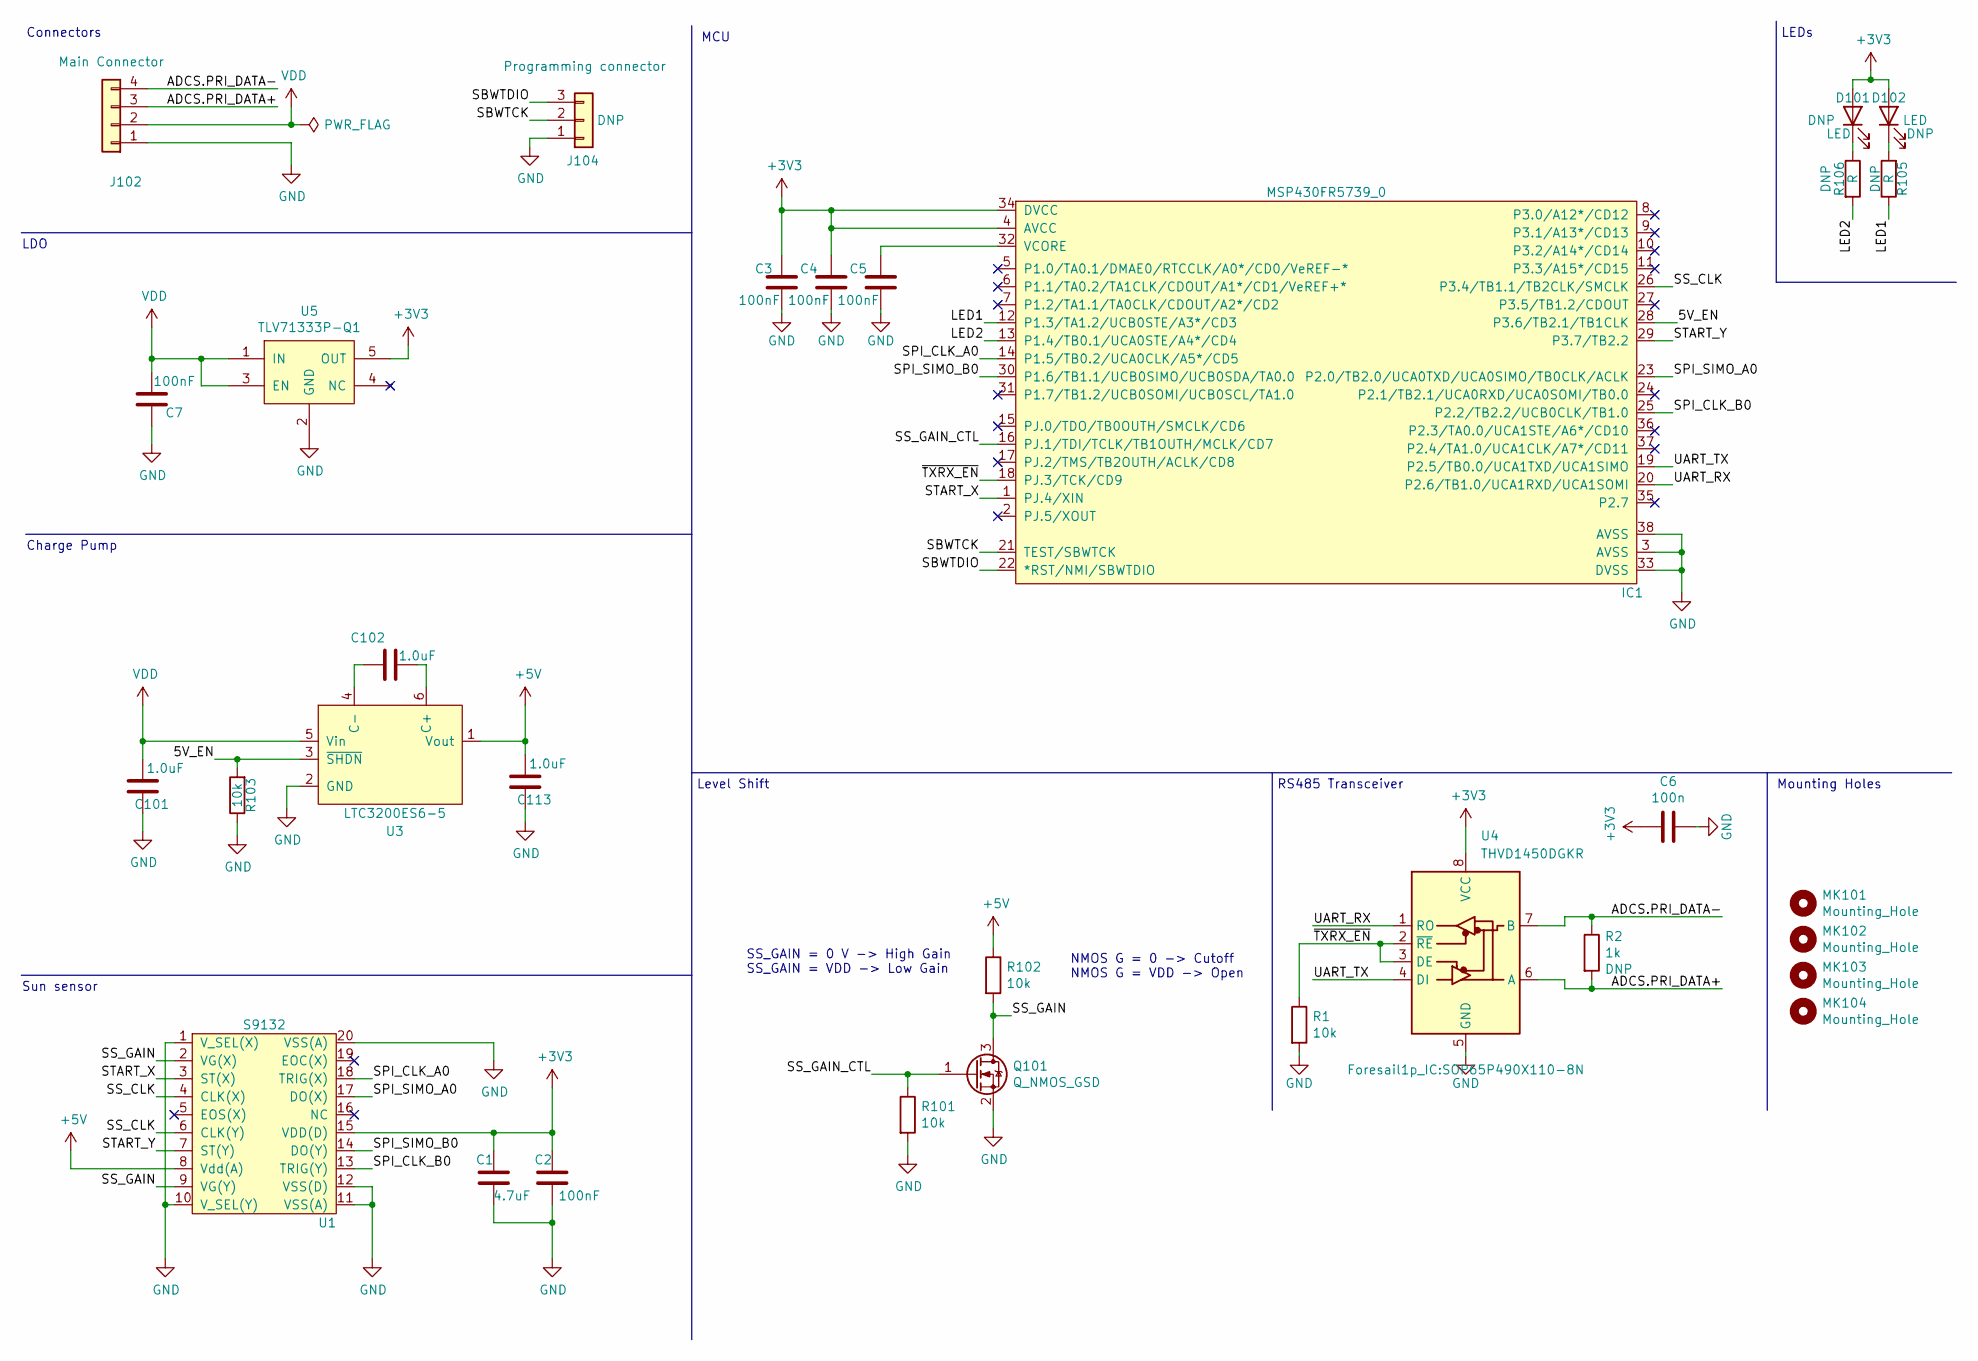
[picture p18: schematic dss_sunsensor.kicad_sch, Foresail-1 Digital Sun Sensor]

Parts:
C1: 4.7uF; C_0603_1608Metric
C2, C3, C4, C5, C7: 100nF; C_0402_1005Metric
C6: 100n; C_0402_1005Metric
C101, C102, C113: 1.0uF; C_0603_1608Metric
D101, D102: LED; LED_0603_1608Metric
IC1: MSP430FR5739_0; TSSOP-38_6.1mm
J102: Main Connector; PinHeader_1x04_P1.27mm_Horizontal
J104: Programming connector; PinHeader_1x03_P1.27mm_Horizontal
MK101, MK102, MK103, MK104: Mounting_Hole; MountingHole_2.2mm_M2
Q101: Q_NMOS_GSD; SOT-23
R1, R101, R102, R103: 10k; R_0402_1005Metric
R2: 1k; R_0402_1005Metric
R105, R106: R; R_0402_1005Metric
U1: S9132
U3: LTC3200ES6-5; SOT-23-6
U4: THVD1450DGKR; SOP65P490X110-8N
U5: TLV71333P-Q1; SOT-23-5; Mouser 595-TLV71333PQDBVRQ1

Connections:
+3V3: C1.2, C2.2, C3.2, C4.2, C6.1, D101.2 (A), D102.2 (A), IC1.4 (AVCC), IC1.34 (DVCC), U1.15 (VDD(D)), U4.8 (VCC), U5.5 (OUT); also elsewhere on the board
+5V: C113.1, R102.1, U1.8 (Vdd(A)), U3.1 (Vout)
/5V_EN: IC1.28 (P3.6/TB2.1/TB1CLK), R103.2, U3.3 (~SHDN)
/ADCS.PRI_DATA+: J102.3, R2.2, U4.6 (A)
/ADCS.PRI_DATA-: J102.4, R2.1, U4.7 (B)
/LED1: IC1.12 (P1.3/TA1.2/UCB0STE/A3*/CD3), R105.1
/LED2: IC1.13 (P1.4/TB0.1/UCA0STE/A4*/CD4), R106.2
/SBWTCK: IC1.21 (TEST/SBWTCK), J104.2
/SBWTDIO: IC1.22 (*RST/NMI/SBWTDIO), J104.3
/SPI_CLK_A0: IC1.14 (P1.5/TB0.2/UCA0CLK/A5*/CD5), U1.18 (TRIG(X))
/SPI_CLK_B0: IC1.25 (P2.2/TB2.2/UCB0CLK/TB1.0), U1.13 (TRIG(Y))
/SPI_SIMO_A0: IC1.23 (P2.0/TB2.0/UCA0TXD/UCA0SIMO/TB0CLK/ACLK), U1.17 (DO(X))
/SPI_SIMO_B0: IC1.30 (P1.6/TB1.1/UCB0SIMO/UCB0SDA/TA0.0), U1.14 (DO(Y))
/SS_CLK: IC1.26 (P3.4/TB1.1/TB2CLK/SMCLK), U1.4 (CLK(X)), U1.6 (CLK(Y))
/SS_GAIN: Q101.3 (D), R102.2, U1.2 (VG(X)), U1.9 (VG(Y))
/SS_GAIN_CTL: IC1.16 (PJ.1/TDI/TCLK/TB1OUTH/MCLK/CD7), Q101.1 (G), R101.1
/START_X: IC1.1 (PJ.4/XIN), U1.3 (ST(X))
/START_Y: IC1.29 (P3.7/TB2.2), U1.7 (ST(Y))
/UART_RX: IC1.20 (P2.6/TB1.0/UCA1RXD/UCA1SOMI), U4.1 (RO)
/UART_TX: IC1.19 (P2.5/TB0.0/UCA1TXD/UCA1SIMO), U4.4 (DI)
/~TXRX_EN: IC1.18 (PJ.3/TCK/CD9), R1.1, U4.2 (~RE), U4.3 (DE)
GND: C1.1, C2.1, C3.1, C4.1, C5.1, C6.2, C7.2, C101.2, C113.2, IC1.3 (AVSS), IC1.33 (DVSS), IC1.38 (AVSS), J102.1, J104.1, Q101.2 (S), R1.2, R101.2, R103.1, U1.1 (V_SEL(X)), U1.10 (V_SEL(Y)), U1.11 (VSS(A)), U1.12 (VSS(D)), U1.20 (VSS(A)), U3.2 (GND), U4.5 (GND), U5.2 (GND); also elsewhere on the board
unnamed: D101.1 (K), R106.1
unnamed: D102.1 (K), R105.2
unnamed: C5.2, IC1.32 (VCORE)
unnamed: C102.1, U3.6 (C+)
unnamed: C102.2, U3.4 (C-)
VDD: C7.1, C101.1, J102.2, U3.5 (Vin), U5.1 (IN), U5.3 (EN); also elsewhere on the board

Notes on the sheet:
Charge Pump
Level Shift
LDO
Sun sensor
SS_GAIN = 0 V -> High Gain SS_GAIN = VDD -> Low Gain
MCU
Mounting Holes
Connectors
RS485 Transceiver
NMOS G = 0 -> Cutoff NMOS G = VDD -> Open
LEDs

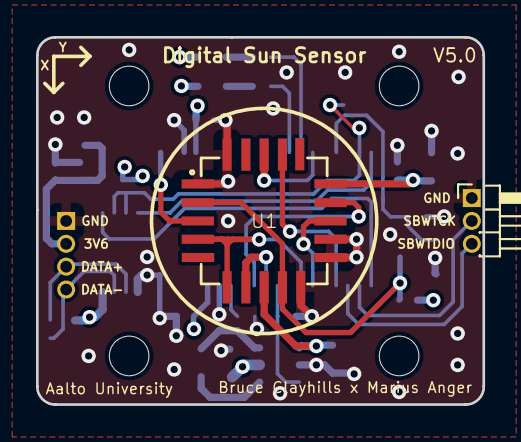
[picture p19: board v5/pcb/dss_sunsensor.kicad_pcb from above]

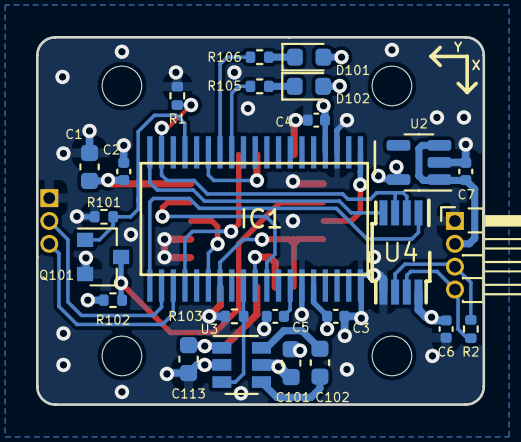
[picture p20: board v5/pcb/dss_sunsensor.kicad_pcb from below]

Board: 4 copper layers, 24.8 x 20.4 mm, 31 parts (25 on the bottom side), 28 nets.

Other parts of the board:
U2: TLV733P; SOT-23-5

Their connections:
+3V3: U2.5 (OUT); also elsewhere on the board
GND: U2.2 (GND); also elsewhere on the board
VDD: U2.1 (IN), U2.3 (EN); also elsewhere on the board

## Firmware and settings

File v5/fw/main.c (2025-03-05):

#include <msp430.h>
#include <stdint.h>

#include "main.h"

#include "telecommands.h"


#include "SPI.h"
#include "DMA.h"
#include "adc.h"

#include "calc.h"

static volatile int interrupt_pending = 0;

////////////////////////////////////////////////////////////////////////////////
/// Platform bus code
////////////////////////////////////////////////////////////////////////////////

#define RS485_PRI_DIR_TX() PJOUT |= BIT3
#define RS485_PRI_DIR_RX() PJOUT &= ~BIT3

typedef struct {
	int active_bus;

	const uint8_t* tx_buf;
	size_t tx_idx, tx_len;

	int slave_rxed;
} BusDriver;

#define BUS_ID_PRIMARY 0

BusFrame* bus_slave_receive(BusHandle* self) {
	BusDriver* driver = (BusDriver*)self->driver;
	if (driver->slave_rxed) {
		driver->slave_rxed = 0;
		return &self->frame_rx;
	}
	return NULL;
}

void bus_slave_send(BusHandle* self, BusFrame* rsp) {
	BusDriver* driver = (BusDriver*)self->driver;

	// Make sure interrupts are disabled. Technically they should
	// be by this point, because bus_slave_send() is called _ONLY_
	// after the slave has received and handled a frame
	UCA1IE = 0;

	// Prepare for transmitting
	const BusFrame* tx_frame = bus_prepare_tx_frame(rsp);
	driver->tx_buf = tx_frame->buf;
	driver->tx_len = tx_frame->len + BUS_OVERHEAD;
	driver->tx_idx = 0;

	// Begin transfer
	// NOTE: TX empty buffer flag needs to be set manually
	if (driver->active_bus == BUS_ID_PRIMARY) {
		RS485_PRI_DIR_TX();
		UCA1IFG = UCTXIFG;
		UCA1IE = UCTXIE;
	}
}

static BusHandle bus_adcs;

#if defined(__TI_COMPILER_VERSION__) || defined(__IAR_SYSTEMS_ICC__)
#pragma vector=TIMER2_B0_VECTOR
__interrupt void bus_rx_timeout_irq()
#elif defined(__GNUC__)
void __attribute__ ((interrupt(TIMER2_B0_VECTOR))) bus_rx_timeout_irq()
#else
#error Compiler not supported!
#endif
{
	TB2CTL &= ~MC__UPDOWN; // Put into stop mode

	bus_adcs.receive_timeouts++;

	bus_reset_rx(&bus_adcs);

	// Enable RX on bus
	RS485_PRI_DIR_RX();
	UCA1IE = UCRXIE;
}

#if defined(__TI_COMPILER_VERSION__) || defined(__IAR_SYSTEMS_ICC__)
#pragma vector=USCI_A1_VECTOR
__interrupt void bus_primary_irq()
#elif defined(__GNUC__)
void __attribute__ ((interrupt(USCI_A1_VECTOR))) bus_primary_irq()
#else
#error Compiler not supported!
#endif
{
	BusDriver* driver = (BusDriver*)bus_adcs.driver;

    switch(__even_in_range(UCA1IV, USCI_UART_UCTXCPTIFG)) {
    	case USCI_NONE: break;
		case USCI_UART_UCRXIFG: { // Receive buffer full
			driver->active_bus = BUS_ID_PRIMARY;

			// Enable receiver timeout timer
			TB2CTL |= MC__UP | TACLR;
			TB2CCTL0 = CCIE;

			if (bus_handle_rx_byte(&bus_adcs, UCA1RXBUF)) {
				// Disable timer
				TB2CTL &= ~MC__UPDOWN;
				TB2CCTL0 = 0;

				// After receiving successfully a frame appointed to our device,
				// disable receiver to make sure rx buffer won't get corrupted.
				// Next function to be called is bus_slave_send().
				UCA1IE = 0;

				// Wake up the main thread.
				driver->slave_rxed = 1;
				interrupt_pending = 1;
				__bic_SR_register_on_exit(LPM0_bits);
			}
		} break;
		case USCI_UART_UCTXIFG: { // Transmit buffer empty
			if (driver->tx_idx < driver->tx_len) {
				UCA1TXBUF = driver->tx_buf[driver->tx_idx++];
			} else {
				UCA1IFG &= ~UCTXCPTIE; // NOTE: must be cleared or ISR will trigger on the previous byte
				UCA1IE = UCTXCPTIE;
			}
		} break;
		case USCI_UART_UCSTTIFG: { // Start bit received
			UCA1IFG &= ~UCSTTIFG;
		} break;
		case USCI_UART_UCTXCPTIFG: { // Transmit complete
			UCA1IE = 0;
			UCA1IFG &= ~UCTXCPTIE;

			// Go to receiver mode on bus
			RS485_PRI_DIR_RX();
			UCA1IE = UCRXIE;
		} break;
		default: break;
    }
}

////////////////////////////////////////////////////////////////////////////////
/// Platform initialization and main loop
////////////////////////////////////////////////////////////////////////////////

volatile uint16_t sys_ticks = 0;

/*
 * Watchdog time configuration
 *
 * Select master clock as the clock source WDT is cleared only in the heartbeat interrupt,
 * so the reset time must be greater than maximum heartbeat period.
 * VLOCLK_frq = 10kHz
 * WDTSSEL__ACLK = 12MHz
 * Reset Time [sec] = (2^X) / CLK_SOURCE
 * See WDTIS for values of X
 * WDTIS__128M (00:00:11 at 12 MHz)
 * WDTIS__8192K (0.699 s at 12 MHz)
 */


#ifdef USE_WDT
#define RESET_WDT() (WDTCTL = WDTPW + WDTSSEL__ACLK + WDTCNTCL + WDTIS__8192K)
#else
#define RESET_WDT() (WDTCTL = WDTPW + WDTHOLD) // Disabled!
#endif

unsigned int idle_counter = ~0;
void reset_idle_counter(){
    idle_counter = 0;
}

// Sleep mode indicator flag. Sleep Mode - 0, Enabled - 1
uint8_t sleep_mode = 1;
void sleep()
{
    // Disable boost converter (AKA shutdown profile sensor)
    BOOST_DISABLE();

    // Disable Start Signal
    ST_SIGNAL_DISABLE();

#ifdef DEBUG
    // Set LEDs off
    LED1_OFF();
    LED2_OFF();
#endif

    // Set sleep mode flag on
    sleep_mode = 1;
}

void wakeup()
{
    // Enable boost converter
    BOOST_ENABLE();

    // Enable Start Signal
    ST_SIGNAL_ENABLE();

#ifdef DEBUG
    // Set LED on
    LED1_ON();
#endif

    // Set sleep mode flag
    sleep_mode = 0;
}


void INTEGRATION_TIMER_INIT(){
    //ACLK set to 12MHz
    //ACLK, UP mode, divide by 1 and 2 --> timer frequency = 12MHz/2 = 6MHz, counter up mode
    TA0CTL = ID__1 + TASSEL__ACLK + MC__UP;
    TA0CCR0 = INT_TIME;                                 // Set the timer/integration time
    TA0EX0 = 0x01;                                      //Divide by 2
    TA0CCTL0 = CCIE;                                    //TACCR1 interrupt enable
    TA0CTL |= TACLR;
}

void HB_TIMER_INIT(){
    /*
     * Configure TimerB0
     *
     * SMCLK = DCO / 1
     * Timer frequency(Hz) = SMCLK / (TB0CCR0 * 8 * 8)
     * TB0CCR0 = SMCLK / (timer_frequency(Hz)*8*8)
     */

    TB0CTL = MC__UP + TBSSEL__SMCLK + ID__8;    // SMCLK, UP mode, divide by 8
    TB0CCR0 = 3000;                             // Count up to this value
    TB0EX0 = TBIDEX__8;                         // Divide by 8
    TB0CCTL0 = CCIE;                            // TBCCR0 interrupt enabled
    TB0CTL |= TBCLR;                            // Clear interrupt
    //CSCTL4 &= ~SMCLKOFF;
    TB0R = 0;
}


/*
 * Timer B0 interrupt (triggering every 16ms) - Used to wakeup the processor and check any new events
 */
#pragma vector=TIMER0_B0_VECTOR
__interrupt void Timer_B0(void)
{
    LED1_TOGGLE();
    sys_ticks++; // sys_tick every 16 ms
    // Wake up the main loop
    //__bic_SR_register_on_exit(LPM0_bits + SMCLKOFF);
    RESET_WDT();
    __bic_SR_register_on_exit(LPM0_bits);
}

static void platform_init() {
	__disable_interrupt();

	WDTCTL = WDTPW | WDTHOLD;

	// Pin configuration
	{
        PADIR=0xffff; PAOUT=0x0000; // Ports 1 and 2
        PBDIR=0xffff; PBOUT=0x0000; // Ports 3 and 4

        //LED 1
        P1SELC &= ~BIT3;                //Select pin 1.3 to I/O
        P1DIR |= BIT3;                  //Select pin 1.3 to output
        P1OUT |= BIT3;

        //LED 2
        P1SELC &= ~BIT4;                //Select pin 1.4 to I/O
        P1DIR |= BIT4;                  //Select pin 1.4 to output
        P1OUT |= BIT4;

        //Start signal X (PJ.4)
        PJSELC &= ~BIT4;                //Select pin J.4 to I/O
        PJDIR |= BIT4;                  //Select pin J.4 to output
        PJOUT |= BIT4;                  //Set start signal high

        //Start signal Y (P3.7)
        P3SELC &= ~BIT7;                //Select pin 3.7 to I/O
        P3DIR |= BIT7;                  //Select pin 3.7 to output
        P3OUT |= BIT7;                  //Set start signal high

        //Set SS clock to SMCLK
        P3SELC |= BIT4;
        P3DIR |= BIT4;

        //Start 5V Boost enable (P3.6)
        P3SELC &= ~BIT6;                //Select pin 3.6 to I/O
        P3DIR |= BIT6;                  //Select pin 3.6 to output
        P3OUT &= ~BIT6;                 //Set Boost off

        // Gain selection (PJ.1)
        PJSELC &= ~BIT1;                //Select pin J.0 to I/O
        PJDIR |= BIT1;                  //Select pin J.0 to output
        PJOUT |= BIT1;                 //Set gain output to low (default)

        // P2.5 = TXD (SEL1.5=1, SEL0.5=0)
        // P2.6 = RXD (SEL1.6=1, SEL0.6=0)
		P2SEL1 |= BIT5 | BIT6;
        P2SEL0 &= ~(BIT5 | BIT6);
	
        // Initialize the RS485 DE/RE pin
        PJDIR |= BIT3;
        PJOUT &= ~BIT3;

		// Disable the GPIO power-on default high-impedance mode to activate
		// previously configured port settings
		PM5CTL0 &= ~LOCKLPM5;
	}

	// Clock configuration
	{
		// Configure one FRAM waitstate as required by the device datasheet for MCLK
		// operation beyond 8MHz _before_ configuring the clock system.
		//FRCTL0 = FRCTLPW | NWAITS_1;

		CSCTL0_H = CSKEY_H; // Unlock

		CSCTL0 = CSKEY;                                        // Password to enable clock manipulation

        //Configure internal crystal (24MHz) as main clock
        CSCTL1 |= DCOFSEL_3 | DCORSEL;                          // Set max. DCO setting 24MHz
        CSCTL2 = SELA__DCOCLK | SELS__DCOCLK | SELM__DCOCLK;    // set ACLK = DC0; MCLK = SMCLK = DCO
        CSCTL3 = DIVA__2 | DIVS__2 | DIVM__1;                   // set all dividers ACLK/2=12MHz, SMCLK/2=12MHz, MCLK/1=24MHz

		CSCTL0_H = 0; // Lock
	}

	// UART reception timeout timer configuration
	{
		TB2CTL = TBSSEL__SMCLK | ID__8 | MC__UP;
		TB2CCTL0 = 0;
		TB2R = 0;
		TB2CCR0 = 399; // 0.2 msec
	}

	// UART configuration
	{
		// UCA1 (primary)
        UCA1CTLW0 = UCSWRST;                    // Set the state machine to reset
        UCA1CTLW0 |= UCSSEL__SMCLK;             // SMCLK (12MHz)

        // 12 MHz 115200 (see msp430fr5739 User's Guide page 491)
        UCA1MCTLW |= UCOS16;                    // Oversampling enabled

        // Proper UART 115200 baud rate
        //UCA1BRW = 6;                            // Set the baud rate to 115200 (12MHz)
        //UCA1MCTLW |= UCBRF_8 | 0x2000;          // Modulation UCBRSx=0x20, UCBRFx=8

        // Baud rate of OBC is 3% (111607) slower AND MESSES UP EVERYTHING
        UCA1BRW = 6;                            // Set the baud rate to 115200 (12MHz)
        UCA1MCTLW |= UCBRF_10 | 0x6B00;          // Modulation UCBRSx=0x6B, UCBRFx=10

        UCA1CTLW0 &= ~UCSWRST;                  // Release the reset
        UCA1IE |= UCRXIE;                       // Enable USCI_A1 RX interrupt

		// Enable RX
		RS485_PRI_DIR_RX();
		UCA1IE = UCRXIE;
	}

    // Initialize WDT
    RESET_WDT();

    /* Basic initalization */
    ADC_INIT();
    SPI_INIT();
    DMA_INIT();                                 //Initialize DMA for SPI data transfer
    INTEGRATION_TIMER_INIT();
    HB_TIMER_INIT();

    __bis_SR_register(GIE); //Enable interrupts
    __no_operation();       // First chance for the interrupt to fire!

    //Boost converter off
    BOOST_DISABLE();

    // Set Sun Sensor Gain to low
    ss_gain(GAIN);

    // Enable the sensor start signal
    ST_SIGNAL_ENABLE();

    // Disable the GPIO power-on default high-impedance mode to activate
    // previously configured port settings
    PM5CTL0 &= ~LOCKLPM5;
}



/*
///////////////////////////////////////////////////////////////////////////////////////////////////////////////////////////////////////////
                                                    Main Loop
///////////////////////////////////////////////////////////////////////////////////////////////////////////////////////////////////////////
*/

static void platform_loop() {
	BusDriver bus_driver = { 0 };
	bus_adcs.driver = &bus_driver;

	for (;;) {

        RESET_WDT();

		// Make sure that all interrupts are serviced before going to sleep
		__disable_interrupt();
		if (!interrupt_pending) {
			__bis_SR_register(LPM0_bits | GIE);
		}
		interrupt_pending = 0;
		__enable_interrupt();

		// Update slave bus
		{
			BusFrame* cmd = bus_slave_receive(&bus_adcs);
			if (cmd != NULL) {
				BusFrame* rsp = bus_get_tx_frame(&bus_adcs);
				handle_command(cmd, rsp);
				bus_slave_send(&bus_adcs, rsp);
			}
		}

        TB0CTL |= TBCLR; // reset hb timer, but is it needed????????????????

        // Processor wakes up every 16ms --> Goes to sleep after 16ms*250 = 4s
        if (idle_counter > 250 && !sleep_mode) {
            // Goto "deepsleep" if UART is not actively used
            sleep();
        }
        else {
            idle_counter++;
            // Resets itself after 16ms*1250 = 20s
            if (idle_counter >= 1250) {

                // Trigger Power-On-Reset (POR) after ~20 seconds of idling
                PMMCTL0 |= PMMSWPOR;
            }
        }
	}
}

int main() {
    platform_init();
    platform_loop();

    return 0;
}

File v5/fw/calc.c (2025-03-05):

#include "calc.h"

#include <stdint.h>
#include <msp430.h>

#include "main.h"
#include "DMA.h"
#include "SPI.h"

/*
/////////////////////////////////////////////////////////////////
                      Dynamic Variables
/////////////////////////////////////////////////////////////////
*/


// SNR variables
uint16_t SNR_X = 0;
uint16_t SNR_Y = 0;

// X and Y position values
int16_t VALUE_X = 0;
int16_t VALUE_Y = 0;

// These are values used for the SNR calculations
uint16_t max_value = 0;
uint16_t min_value = 0;

// These indexes are used to save the location of the point where we went over the saturation level
uint8_t low_index = 0;
uint8_t high_index = 0;
uint8_t max_index = 0;

const static uint8_t INTERVAL = 3;                       // This is for the rolling average calculation. Set to 5 by default, must be UNEVEN
const static uint8_t SHIFT = 2;                          // Shift is used in rolling average, for the array correction. Set to 2 by default formula SHIFT = ((INTERVAL-1)/2)
const static uint8_t SCALE = 8;                          // This is used for the Quadratic middle calculation. Set to 8 by default

// This flag is used to indicated whether or not data is requested by the I2C handler
volatile uint8_t dataRequested = 0;


/*
/////////////////////////////////////////////////////////////////
                         FRAM Variables
/////////////////////////////////////////////////////////////////
*/

#pragma SET_DATA_SECTION(".fram_vars")
// Sensor raw data arrays
uint8_t x_data[256];
uint8_t y_data[256];


// FRAM variables and constants
int16_t X_BIAS = 0;                  // This value is multiplied by 8, to compensate for the scaling factor SCALE (127.5-143.26)*8 = -126
int16_t Y_BIAS = 0;                    // This value is multiplied by 8, to compensate for the scaling factor SCALE (127.5-128.02)*8 = -4
// Temperature BIAS
int16_t TEMPERATURE_BIAS = 0;           // temp bias in deciDegC

uint16_t VALUE_Z = 1;                   // height

uint16_t INT_TIME = 3200;              // This is the integration time variable. Tint = 1/0.75MHz*INT_TIME
uint16_t SAMPLING_TIME = 3200;         // This is the amount of clock ticks it takes to sample the sensor one time MUST BE OVER 3200

// This is the saturation level of the sensor. This value is used to determine when the data is saturated and what algorithm is used to estimate the center spot
// The saturation level is calculated with the interval and value between 0-250. I.e. a saturation level of 240 would be SAT_LEVEL = 240*INTERVAL(2) = 480
uint16_t SAT_LEVEL = 100;

// This is the gain of the Sun Sensor which is saved in FRAM
uint8_t GAIN = 0;

#pragma SET_DATA_SECTION()

// This is used to determine the time during which a DMA transfer should have occured
uint16_t TIMEOUT_TIME = 3500;                  // Timeout time

volatile int int_flag = -1;

#pragma vector=TIMER0_A0_VECTOR
__interrupt void INTEGRATION_TIMER_ISR(void)
{
    INTEGRATION_TIMER_DISABLE();

    switch (int_flag)
    {
    case 0: {

        // Set INTEGRATION period and clear timer
        TA0CCR0 = INT_TIME;
        TA0CTL |= TACLR;

        // Pull start pins up
        START_PINS_UP();

        // Enable the integration timer
        INTEGRATION_TIMER_ENABLE();

        int_flag = 1;

        break;
    }

    case 1: {
        if (dataRequested == 1) {

            // Clear DMA interrupts
            DMA0CTL &= ~DMAIFG;
            DMA1CTL &= ~DMAIFG;

            // Reset SPI and DMA
            SPI_RESET();
            DMA_INIT();

            dataRequested = 2;
        }

        // Set INTEGRATION period and clear timer
        TA0CCR0 = TIMEOUT_TIME;
        TA0CTL |= TACLR;

        // Pull start pins down
        START_PINS_DOWN();

        INTEGRATION_TIMER_ENABLE();

        int_flag = 2;

        break;
    }
    case 2: {
        if (dataRequested == 2) dma_timeout = 1;

        ST_SIGNAL_ENABLE();

        break;
    }

    default:{
        // Disable the integration timer
        INTEGRATION_TIMER_DISABLE();

        break;
    }
    }
}

int SAMPLE_SENSOR()
{

    dataRequested = 1;

    while(1){
        if((DMA_x_flag == 1 && DMA_y_flag == 1) || dma_timeout){

            // Reset data request variable
            dataRequested = 0;

            // Disable the DMA and SPI controllers
            SPI_DISABLE();
            DMA_DISABLE();

            // Set DMA x and y flags to zero, so that they're ready for the next read
            DMA_x_flag = 0;
            DMA_y_flag = 0;

            // Check to see if we sampled the sensor or if a timeout occured
            if (dma_timeout != 0){
                // Reset DMA timeout flag
                dma_timeout = 0;
                return 0;
            }

            // Reset DMA timeout flag
            dma_timeout = 0;
            return 1;
        }
    }
}


/* Start signal enable function. This function is used to send the
 * start signals continuously to the sensor.*/
void ST_SIGNAL_ENABLE(void)
{
    // Initialise interrupt flag
    int_flag = 0;

    // Set SAMPLING period and clear timer
    TA0CCR0 = SAMPLING_TIME;
    TA0CTL |= TACLR;

    // Disable DMA interrupt
    DMA0CTL &= ~DMAIE;                                   //DMA interrupt disable
    DMA1CTL &= ~DMAIE;                                   //DMA interrupt disable

    // Pull start pins down
    START_PINS_DOWN();

    // Start SAMPLING TIMER
    INTEGRATION_TIMER_ENABLE();
}


void ST_SIGNAL_DISABLE(void)
{
    // Disable the integration timer
    INTEGRATION_TIMER_DISABLE();

    // Set the interrupt switch case variable to -1
    int_flag = -1;
}
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

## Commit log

2025-03-05 pushed v4 and v5 similar to psd
    [digital_sunsensor.step, dss_sunsensor.kicad_pcb, dss_sunsensor.kicad_sch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]
2026-03-24 Update README with performance article link
    Added a link to the performance and testing article for the DSS sun sensor.
